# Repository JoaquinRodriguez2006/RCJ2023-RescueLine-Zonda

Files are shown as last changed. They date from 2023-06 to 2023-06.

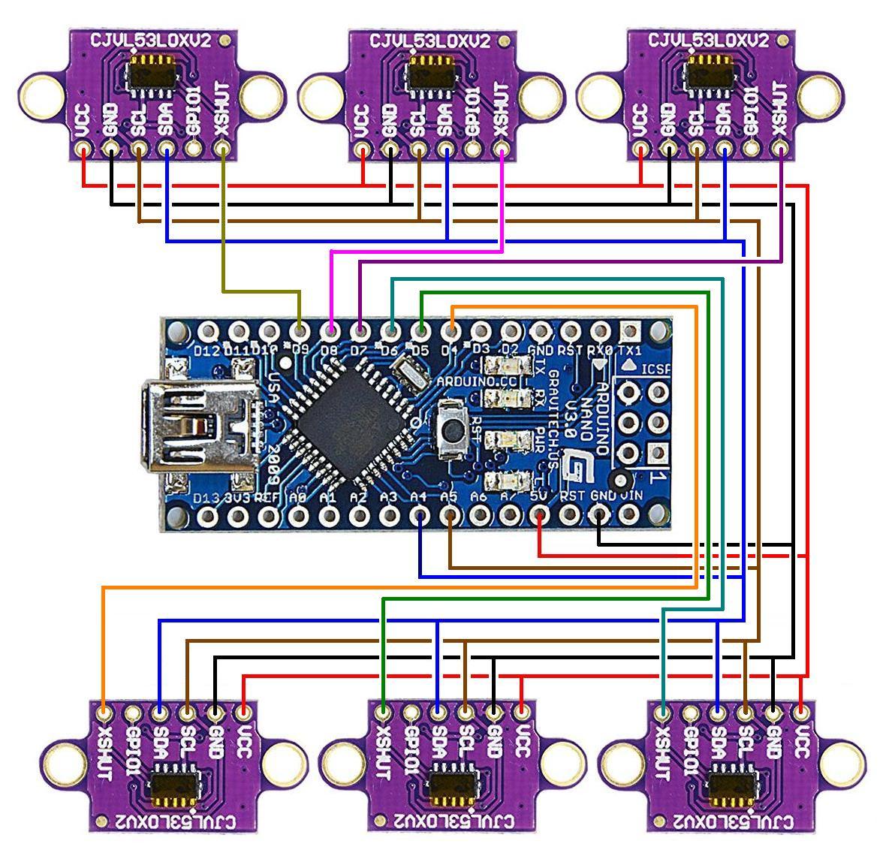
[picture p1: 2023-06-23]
Ejemplos Tof/Ejemplos usados/VL530X multi/VL530Xmulti.jpeg

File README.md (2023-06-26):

# Welcome to Team Zonda's Repo!
Hi there! We are Joaquín Rodríguez and Joaquín Argañaraz, from team Zonda IITA Salta, and we are excited to share our project with you! We are taking part in RCJ2023-RescueLine, and decided to create a robot that would push the limits by improving our Lego Spike Prime robot as much as possible. To do this, we developed a communication protocol between the Lego Spike and an Arduino Nano, which controls four Time-of-Flight sensors used to detect obstacles and walls, as well as some servos that operate the claw we use to pick the victims up! For further details, check out our Team Description Paper down below:

TDP Zonda: [tdp_zonda.pdf](https://github.com/JoaquinRodriguez2006/RCJ2023-RescueLine-Zonda/files/11843032/tdp_zonda.pdf)

or, to see the whole development process, feel free to look for anything you might need in our Engineering Journal!

Engineering Journal Zonda: [ZondaTeam.EngineeringJournal.pdf](https://github.com/JoaquinRodriguez2006/RCJ2023-RescueLine-Zonda/files/11843184/ZondaTeam.EngineeringJournal.pdf)

From codes to custom boards, everything in this project is open source and we hope you can feel inspired by it and contribute or replicate it and improve it on your own!! We would love to see this project and the innovations it features implemented in your robots!! Keep in mind, however, that this repo is under an MIT License, which gives you access to everything, yet asks you to give credits to the creators.

## Components
In order to make this possible, we are using electronic components, 3D-designed pieces and a Lego Spike robotics kit.

### Electronic Components
- Arduino Nano
- 4 Time-of-Flight sensors
- Standard Servo
- Mini Servo
- Custom board for Arduino Nano
- 2 custom boards for Time-of-Flight sensors (can hold up to 3 of them each, though we are only 2 on each side)
(Boards available at ```Placas Robotica``` )

### 3D Pieces
- Standard Servo Support
- MiniServo Support
- Claw (Left part & Right part)
- Adaptor Lego stick - servo
- Battery mount
- Claw Gears (Left & Right)

(You can check the .stl files here: ```3D Designs``` )

### Lego Spike Prime
- Lego Spike Prime educational robotics kit

## Codes
As we are using two different boards, two different codes are needed. The Lego Spike is coded in Python, while the Arduino uses C++. If you want to see the explanation of each code, function by funtion, feel free to check it out here: ```Documentation/Zonda IITA Salta. Codes/explanation.txt```
### Lego Spike Code
Uses Python and controls color sensors, motors and sends instructions to the Arduino, specifying what to do.
### Arduino Nano Code
Uses C++ and controls Time-of-Flight sensors and the servos operating the claw.

## PID Controller

## Communication Protocol

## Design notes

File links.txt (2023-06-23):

Lugares para indagar:

(Identificacion de pines)
https://www.facebook.com/groups/SPIKEcommunity/posts/1168406093537621/?mibextid=HsNCOg

(Documentacion pines)
https://github.com/GianCann/SpikePrimeHub

(I2C pins for arduino)
https://www.instructables.com/I2C-between-Arduinos/

(Raspberry HAT para controlar cosas de spike)
https://www.raspberrypi.com/news/raspberry-pi-build-hat-lego-education/

(conexion entre arduino y NXT)
https://www.dexterindustries.com/howto/connect-the-arduino-and-the-lego-mindstorms-together/

(conexion UART spike libreria)
https://antonsmindstorms.com/2022/11/18/lms-esp32-tutorials-part-0-how-to-get-started/

(libreria UART Remote arduino)
https://uartremote.readthedocs.io/en/latest/arduinouartremote.html

(MPY robots Tools)
https://github.com/antonvh/mpy-robot-tools

(conexion I2C entre EV3 y arduino)
https://www.dexterindustries.com/howto/connecting-ev3-arduino/

(I2C scanner)
https://playground.arduino.cc/Main/I2cScanner/

(Links utiles y conexion entre Raspberry Pico y Spike)
https://github.com/justMega/spikeResources

(Documentacion completa de Spike)
https://hubmodule.readthedocs.io/en/latest/port/

(Documentacion extra de Spike)
https://lego.github.io/MINDSTORMS-Robot-Inventor-hub-API/class_usb_vcp.html

(Conexion bluetooth entre Spikes y Raspberry)
https://github.com/bricklife/LEGO-Hub2Hub-Communication-Hacks

(Conexion bluetooth en mas profundidad)
https://github.com/maarten-pennings/Lego-Mindstorms

(Video Rasbperry Pi Zero y Spike)
https://www.youtube.com/watch?v=K0kwiPHDSnw

(Spike Comunication)
https://github.com/PhoBricks/SPIKE_communication

(Hub2Hub BLE)
https://www.facebook.com/groups/SPIKEcommunity/posts/1322920758086153/

(Documentacion Hub2Hub)
https://hubmodule.readthedocs.io/en/latest/hub2hub/

(Muchos Tutoriales con Arduino)
http://robojax.com/learn/arduino/

(Usar 2 VL53L0X (no lo usamos por mucho consumo de memoria))
http://robojax.com/learn/arduino/?vid=robojax_VL53L0X_multiple

(Usar 4 VL53L0X (no lo usamos por mucho consumo de memoria))
http://robojax.com/learn/arduino/?vid=robojax_VL53L0X_multiple_4

(I2C Scanner)
http://robojax.com/learn/arduino/?vid=robojax-I2C-scanner

(Usar 6 VL53L0X)
https://arduinoproyek.wordpress.com/2019/03/27/vl53l0x-multi-sensor/

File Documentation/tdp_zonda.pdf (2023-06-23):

ZONDA IITA SALTA | 1

# RoboCupJunior Rescue Line 2023

# Team Description Paper

## Zonda IITA Salta

Joaquín Rodríguez – Joaquín Argañaraz

Abstract – We are taking part in the Rescue Line category, where the robot needs to follow a line, avoiding any obstacles that may appear and turning left or right according to green tapes on the floor, until it reaches a rescue area. In this part, the robot will have to identify and classify alive and dead victims and rescue them, leaving them in a red or green corner located in the square. Our robot is able to do this efficiently and in record-breaking time (compared to previous versions of our project). This year, we took things way further and decided to use a Lego Spike kit, though we developed a communication protocol between the Spike and an Arduino Uno. This way, we couldn’t use Lego pieces only, and our robot features servos, 3D pieces and Time of Flight sensors, something never seen before.

I. INTRODUCTION
A. Team

Our team is rather small: it consists of only two people: Joaquín Rodriguez and Joaquín Argañaraz. We were both born in Salta and have been taking robotics classes since 2018 and 2017 respectively. Joaquín A. has taken part in RoboCup Junior 2019, in Australia, and has vast experience in educative robotics, as he’s been improving his skills and techniques over the years. He took part in Roboliga Nacional 2017 – Rescue Line, in Roboliga Nacional 2018 – Rescue Line, which took place in San Luis, Argentina, resulting in the first place, in Roboliga Nacional 2019 and in Roboliga Nacional 2022 – Rescue Line, with Zonda Team, which resulted in the first place and was able to represent Argentina in RoboCup Junior 2023. Joaquín Rodríguez, on the other hand, took part in Roboliga Nacional 2021 – Rescue Simulation, in RoboCup 2022 – Rescue Simulation, resulting in the 6th place and obtaining a Prize for the Best Teamwork. He also took part in Roboliga Nacional 2022, with Zonda Team, resulting in the first place, which lets the team represent our country in this competition.

II. PROJECT PLANNING

A. Overall Project Plan

Our aim for the competition is to improve the robot we’ve been building since September 2022. That original version of our project was able to navigate the whole scenario smoothly and with no complications at all. Nonetheless, we wanted to take things to the next level. We believe there was much more job to get done, so that is what we did. Our plan was to keep using Lego Spike for the main structure of the robot, yet we figured that some of its features didn’t live up to our expectations; we wanted a more precise distance sensor and a more professional claw. Keeping those things in mind, we realized that, even though Spike could perform such tasks, a dedicated tech pieces would do a better job. Therefore, we 3D printed a claw that would fit perfectly in our robot and bought Time of Flight sensors to replace the original Lego Spike distance sensor. To control all this gear, we initially intended to use a Teensy 4.1, which was impossible due to time issues. Therefore, we used an Arduino Nano instead.

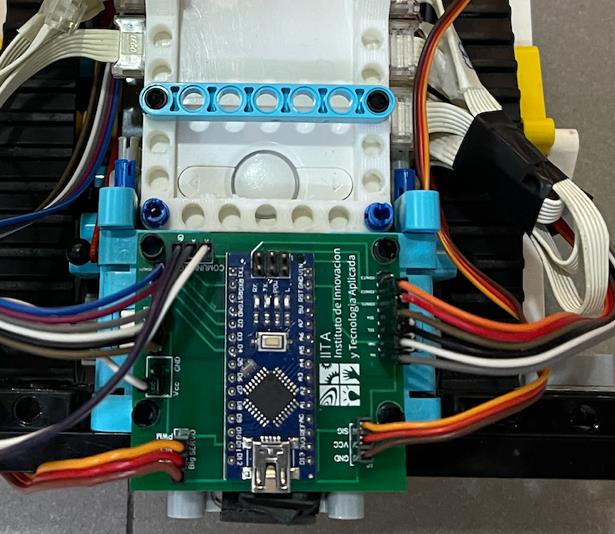
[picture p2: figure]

Fig.1: Arduino Nano fixed to the board.

Our plan was to use Lego Spike and Arduino Nano all together, integrated with each other, communicating both boards with a communication protocol of our own. Using a Lego minicomputer along with another board is something that none of us has ever seen before and we’re sure that, this could open a whole new world of possible things for our robot.

Apart | from | integrating | all | those
improvements to the project, there were some issues in the PID controller the robot uses to follow the line, so it was important to fix that as soon as possible.

Even though we are conscious the task the robot has to go over is rather complex and requires time and preparation, when we decided how to face this exercise, we chose to be ambitious. Time is not on our side and, in fact, is becoming a problem there is not enough time to implement everything we wanted on our robot. To begin with, we are choosing the first victims corner option, which is 0.5 cm tall instead of the second option, with 6cm of height. The original plan was to choose the second one, and the hardware selection was made according to that initial decision. Nonetheless, the robot would have needed a new color sensor to detect the wall and identify if it was red or green, which, even though was a good idea, couldn’t be implemented, as there are no free ports and there was literally no space for a new sensor.

Another important thing regarding our strategy is the rescue kit the robot has to pick up from the side of the line. We are going to have it put next to the line instead of carrying from the beginning of the task. Despite still not working properly and having very little time to fix it, our robot contains the necessary hardware to identify the cube and its claw is designed in a way that allows it to pick up the ball. Carrying the rescue kit from the beginning sounds logic and might be, in fact, a much cleverer idea. However, many pieces of the robot were designed specifically to be able to solve these kinds of situations and we want to show that.

B. Integration Plan

Our robot could be organized in various aspects: electronics, software, and hardware. The integration between all these areas is seamless and is barely noticeable, as we have organized everything in such a way that by pressing just a single button and connecting a single cable, it’s possible to get everything operating together.

We are working with a Lego Spike and an Arduino Nano, which means we have to establish some sort of connection between the two. To do so, after some time researching, we found out that it is possible to connect a Lego device to an Arduino board using a distance or color sensor, being the Lego Spike the host of the connection and the Arduino the slave, which was perfect for what we had planned. To establish such connection, we had to tear down a Lego Spike Distance Sensor and connect one side of the cable to the Arduino. Then we connected the Distance Sensor cable to the Spike. This way, the Arduino is able to send and receive messages to and from the Spike. Even though it is possible for the buffer to fill up and cause a lag between what the Spike is sending and what the Arduino is reading, this did not happen due to the implementation of a function that makes each board send messages only once, and not many times.

III. HARDWARE

A. Mechanical Design and Manufacturing

Lego Spike:

Our robot is built on a chassis made by Lego Spike pieces. From the caterpillars to the supports for the Spike Hub and the Arduino Nano, we have used the Lego Spike normal pieces that come in the box when it is first purchased, as it simplifies the building process, while still providing a reliable and solid base on which the other parts of the robot can be held.

3D Pieces

Apart from using the Lego Spike pieces that came with the robotics kit, we designed and printed many 3D pieces in our attempt to improve the claw mechanism.

Firstly, this robot features a claw (Fig.
2) that allows it to pick the victims and the rescue kit with no problems at all, thanks to its big lip at the bottom. This claw was not made by us; we found the design online (ap. 1) and decided to use it. however, the claw on the robot isn't the same as the one on the Internet. In fact, it looks like a completely different piece, as we've modified it in order to make it more functional to our needs. The changes include: 1) a lip that helps it pick up the rescue kit, 2) an increase in the height of the upper part of the claw (the claw wasn't long enough, and it didn't reach he ground, which made the process of picking the ball and the cube up a lot more complicated. Therefore, even though we could've made the claw a little bit taller, we decided to add some inches in the upper part, as it was the one that would mean the least increase in weight) and 3) reinforcements of certain pieces that are likely to break, like structural slim sticks and the part of the claw where we screw it to the main structure, as it was too tall, but too thin.

Fig. 2: The completely redesigned claw the robot features. It has a big lip at the bottom. It is 9 mm height, which, according to our measurements, is the biggest the down lip can be in order to be able to pick the ball up smoothly while still being able to lift the rescue kit: the servo makes pressure, and the down lips provide with enough surface for the cube to be lifted while being kept tight between the two claws. When the claw is lifting, the rescue kit eventually falls into the claws.

The claw is mounted on a 3D-designed support that does not only support the claw, but also the servo that operates the whole lifting and lowering mechanism. This piece was completely designed by us, and, even though exact measurements were taken, many versions had to be made in order to find the

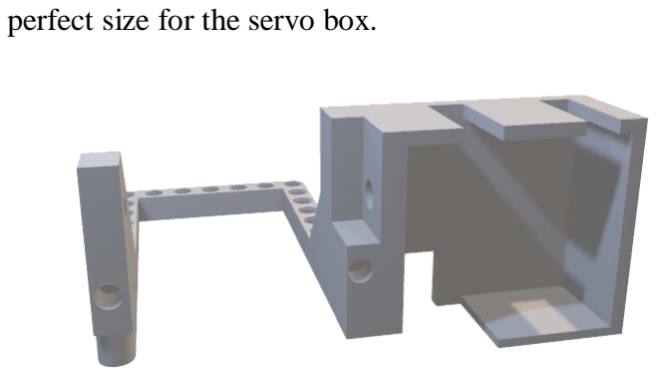
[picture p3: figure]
perfect size for the servo box.

Fig. 3: Standard Servo Support holds the standard servo, which is responsible of controlling the lifting and lowering of the claw. Hence, the piece has space for a horizontal stick that will receive the rotation of the servo and help with the movement of the claw.

Fig. 4: Adaptor that connects the horizontal stick to the servo.

We needed a piece to hold the servo that opens and closes the claw, as well as the claw itself. This piece needed to be strong, yet not too heavy, as it had to be able to be lifted and lowered by the standard servo. Keeping this in mind, we designed a piece that would have these requirements. This piece is rather long, helping the claw be a little separated from the robot’s structure when lowered, and contains a small box that holds the servo, as well as interlocking joints to place the gears that help with the claw’s movement.

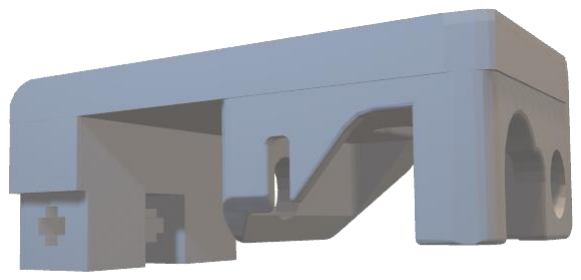
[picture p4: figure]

Fig. 5: Small Servo Support holds the small servo in a personalized servo box that keeps the small digital servo tight and ready to operate the claws. It also has little reliefs at the back so that the gears can fit in perfectly.

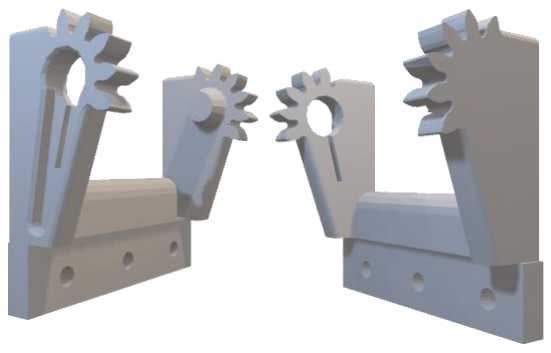
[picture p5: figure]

Fig. 6: The claw gear mechanism that allow it to open and close.

B. Electronic Design and Manufacturing

We are using two main types of sensors: three Lego Color Sensors and four Time of Flight sensors. Despite being used simultaneously, they are not controlled by the same board. The Lego Spike controls the Color Sensors and the Gyroscope and the Arduino Nano controls the ToFs sensors. In order for these two boards to work together, we needed to establish an Universal Asynchronous Receiver-Transmitter (UART) connection between them, which is possible after connecting Spike TX to Arduino RX and vice versa.

Lego Spike
Spike is the main board we are using and the host of the connection Spike-Arduino. The Lego Spike receives and sends information to the Arduino using one of its sensor cables. We had to cut a Distance Sensor cable in order to have access to the pins.

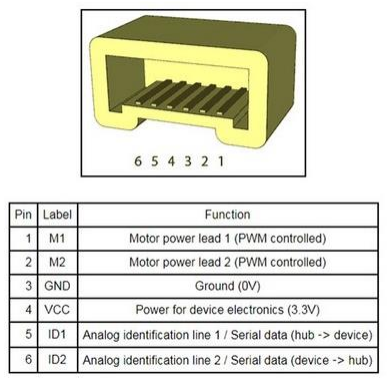
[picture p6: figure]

Fig. 7: Lego cable pinout

The pins include two PWM pins, two alimentation (VCC – GND) pins and two communication pins. The pins we are using for communication are RX, TX and GND. The pins in the cable are connected to Arduino RX, TX and GND (switching RX in the Lego cable to TX in the Arduino and RX in the Arduino to TX in the Lego cable). By doing this, we are able to send and receive information from and to the Arduino and Spike without clutter, as we’ve implemented a message request – answer system that we will explain in detail later.

Also, aiming to create a robot that isn’t completely full of disorganized cables and non-safe connections, we designed a board to hold the Arduino Nano and facilitate the connection with the Lego cable.

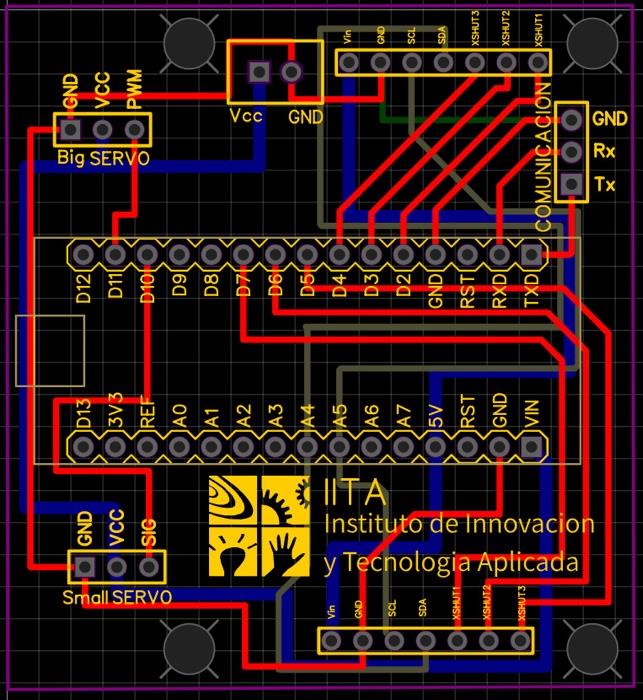
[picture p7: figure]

Fig. 8: The board that holds the Arduino in the middle and receives the cable connections on the sides.

Regarding sensors, we are using three Lego color sensors, which are symmetrically arranged under the robot.

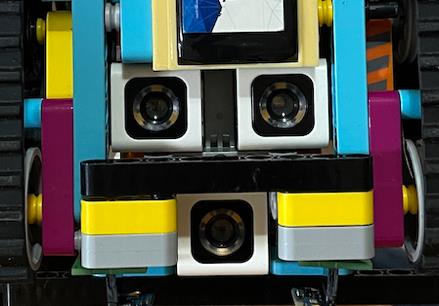
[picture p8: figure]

Fig. 9: Color sensors under the robot.

To detect things, we implemented a new technology for us, which is Time of Flight sensors (ToFs). They are fixed to a personalized board located in the front part of our robot.

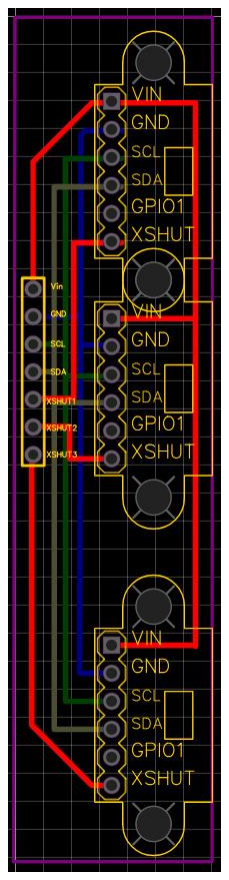
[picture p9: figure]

Fig. 10: Board that holds the Tine of Flight sensors. There are three spots for a ToF sensor, yet we are only using two and planning to add a third one in the future.

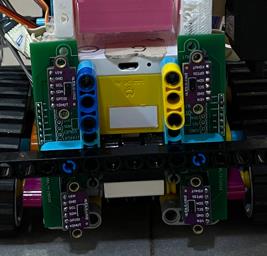
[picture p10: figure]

Fig. 11: Time of Flight boards located at the front of our robot.

IV. SOFTWARE

A. General Software Architecture

We have coded our robot in two different languages: we used Python for the Lego Spike and C++ for the Arduino Nano.

As we mentioned earlier, our robot consists of two different boards that need to communicate wirily. Hence, codes should be able to read the buffers, so as to know if there is anything it needs to know, and also send messages to the other board using a specific communication protocol. This communication protocol is explained in detail in the diagram below:

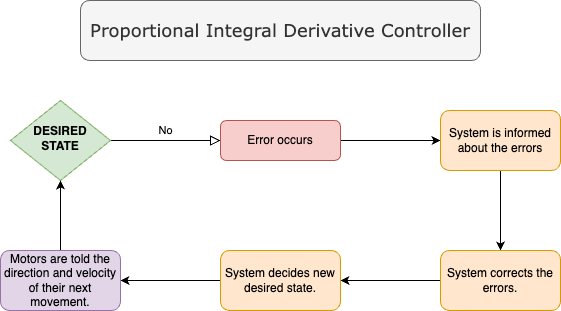
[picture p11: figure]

Diagram 1: Communication Protocol

Python Code
Our Python code is used in the Lego Spike Hub, which controls the motors and receives and process information from three Color Sensors and is responsible for the whole line-following part of the exercise, except for the obstacle, that needs the Time-of-Flight sensors. The algorithm used to follow the line
is | the | Proportional-Integral-Derivative
Controller (PID Controller) (Appendix, 1)

C++ Code
The C++ code operates the servo and receives and process the Time-of-Flight data. This code reads the state the Lego sends via UART messages and starts sending the Spike letter, depending on the state, according to what the sensors are seeing, (STATE = ‘line-follower’ → a: ‘go’, f: ‘stop’) (STATE = ‘obstacle’ → N: ‘nule’, R: ‘super close’, C: ‘close’, M: ‘very far’, L: ‘far’) (STATE = ‘rescue’ → U: ‘nule’, N: ‘near’, F: ‘far’). It also reads if the Spike has sent an order and, depending on the message the Lego Hub sends, lifts, lowers, opens, or closes the claw.
B. Innovative Solutions

UART Communication Protocol Arduino - Spike
A communication protocol between two completely different microcontrollers was implemented. Keeping in mind that it was necessary to connect those boards seamlessly, establishing a clean connection that would not clutter neither the Arduino
nor | the | Spike | buffers, | an | UART
communication protocol was developed. As it is known, UART connections use
serial | ports | to | receive | and | send
information. Therefore, knowing that both boards had to be capable of sending and receiving info, so as to maintain a human-like conversion, though not only using
complete | phrases, | sentences | and
paragraphs, but uppercase and lowercase letters in order to transmit instructions or states. As it has been stated before, the two boards are connecting via serial ports using
RX, | TX | and | GND | pins. | The
communication | protocol | is | possible
because of a Lego Distance Sensor cable that has been cut, so that the connector that goes right in the Lego Spike Hub could be on one side of the cable (allowing it to connect to the hub like a normal sensor) and the pins could be ready to be plugged in the Arduino Nano. This way, the Arduino functions almost like a normal sensor (or at least that is how the Spike understands the information it sends), except for the fact that, of course, must be coded in a different language and that it is not, by all means, a normal sensor. It could be considered a ‘mega-Lego-sensor’, as it is in charge of many important tasks: operating everything related to the claw

(opening, closing, lowering and lifting it) and checking the robot does not crash into obstacles or walls by controlling the data collected by Time-of-Flight sensors. This communication protocol is also effective due to the highly-debugged code, which has a function that prevents buffers from cluttering with messages.

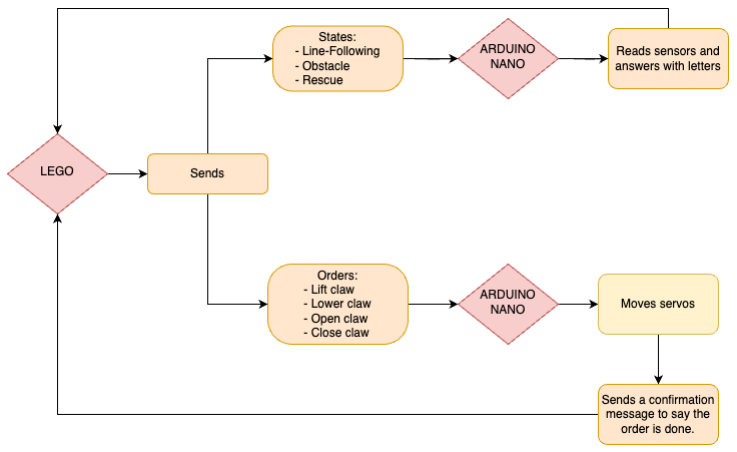
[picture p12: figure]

Diagram 2: Communication Protocol.

### Integration

In order to make this integration even better, the Arduino is not working alone; many Time-Of-Flight sensors depend on it, as well as two servos located above and at the side of the claw. For us to integrate those non-Lego pieces into the design and aesthetics of the main structure, it was necessary to adapt some pieces. Therefore, some crucial parts of the robot, such as the claw mount, are fixed to the Lego Brick because they have been 3D-Printed, and the design met Lego measurements and sizes.

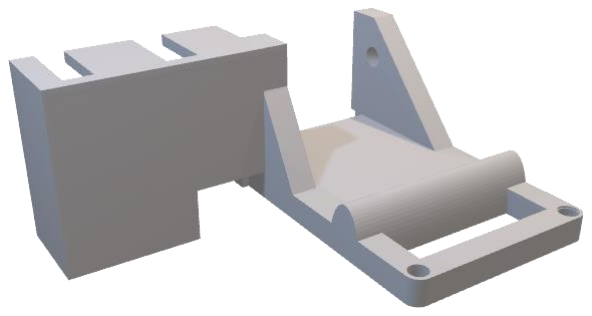
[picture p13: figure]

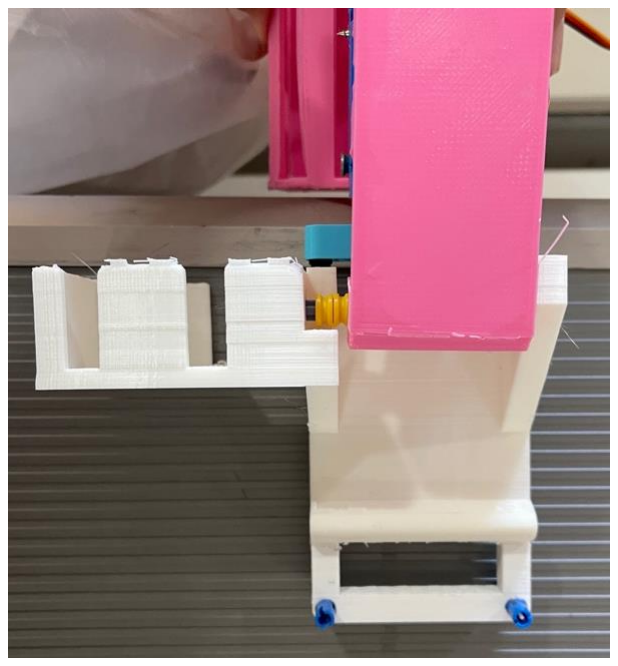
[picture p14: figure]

Figs. 12 & 13: The claw mount that is fixed to the Lego Brick

V. PERFORMANCE
EVALUATION
Our robot is able to follow the line slowly, though precisely and never steps out of
line. | Obstacles, | ramps, | seesaws,
speedbumps are solved. It is also able to deposit the Rescue Kit in the rescue area in a decent way. Even though it sometimes struggles with ramps, it is sure that the robot will overcome it. The most complicated part is, for sure, the rescue area, which is still under testing. Zonda IITA Salta robot is able to identify victims, rescue and deposit them in a corner with no complications. However, we did not add anything so as for the robot to be able to know whether it is an alive or a dead victim. Nonetheless, it recognizes red and green corners and it chooses where to deposit one victim or the other using a random() function.

VI. CONCLUSION
To sum up everything that has been stated so far, Zonda IITA Salta robot is able to follow the line seamlessly and with no complications, except for the ramp, sometimes. This robot is innovating by
including | a | Lego | – | Arduino
communication protocol which allows both boards to work together by sending and receiving messages that command states or orders. Also, we are implementing a new technology for us, which are Time of Flight sensors. In order to integrate them to the general structure of the robot, we designed boards, which are not exclusive for ToFs. There is also a custom board for the Arduino Nano. These boards help with cable management, as there are not disorganized cables around the robot, and also with safety, due to the fact that these cables connected to the boards will not fall off, causing problems.

This is, overall, a good, reliable robot that might be a little slow sometimes, but it is surely going to perform decently.

REFERENCES

- https://scholar.google.com/scholar_url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 (https://scholar.google.com/scholar_url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)
- https://en.wikipedia.org/wiki/PID_controller
- http://ethesis.nitrkl.ac.in/5405/1/109EI0326.pdf
- https://www.ni.com/es-cr/shop/labview/pid-theory-explained.html
- https://www.analog.com/en/analog-dialogue/articles/uart-a-hardware-communication-protocol.html
- https://www.circuitbasics.com/basics-uart-communication/
- https://www.geeksforgeeks.org/universal-asynchronous-receiver-transmitter-uart-protocol/

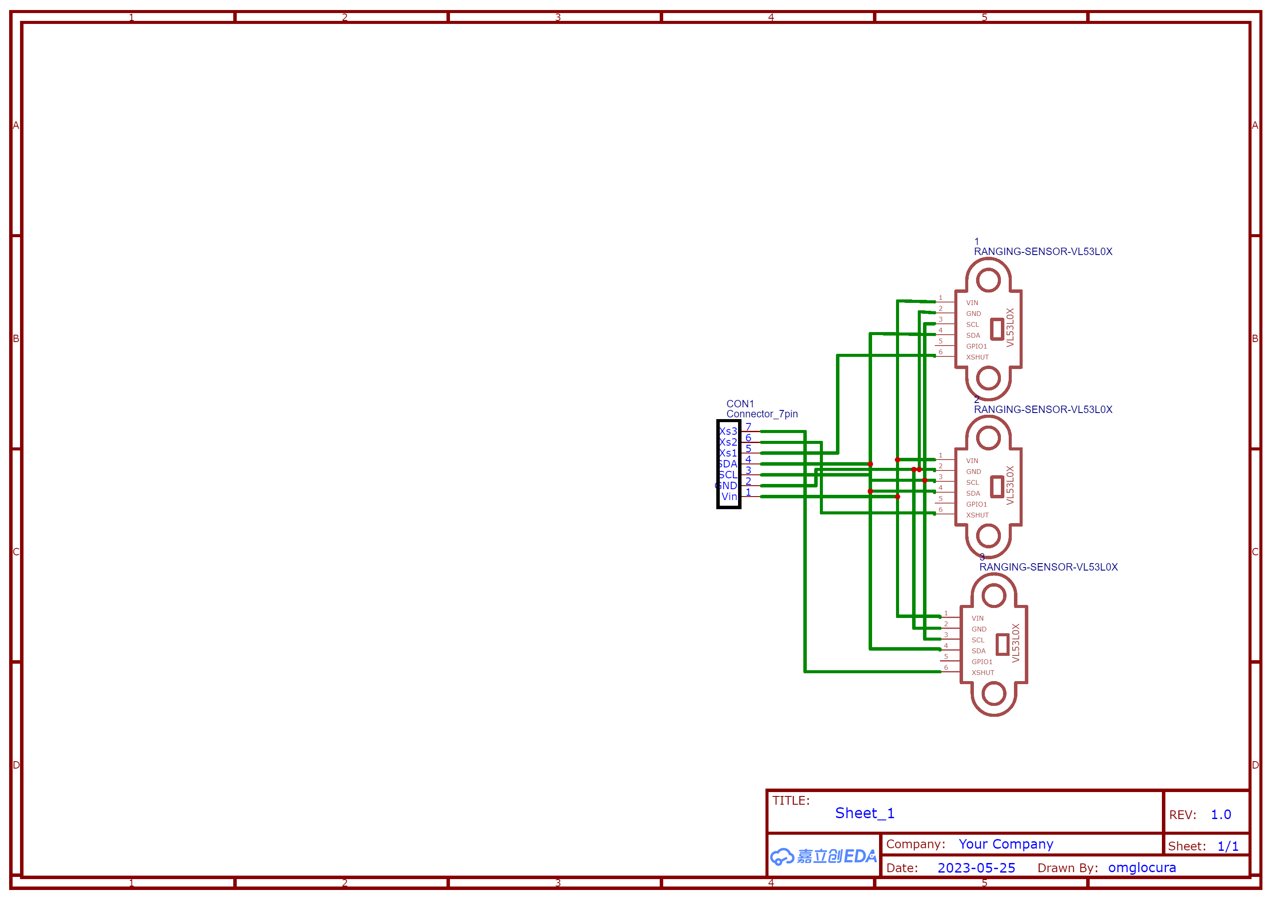
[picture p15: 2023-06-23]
Placas Robotica/PCB ToF/Schematic_Pcb Tof Robocup Joaquin_2023-06-20.png

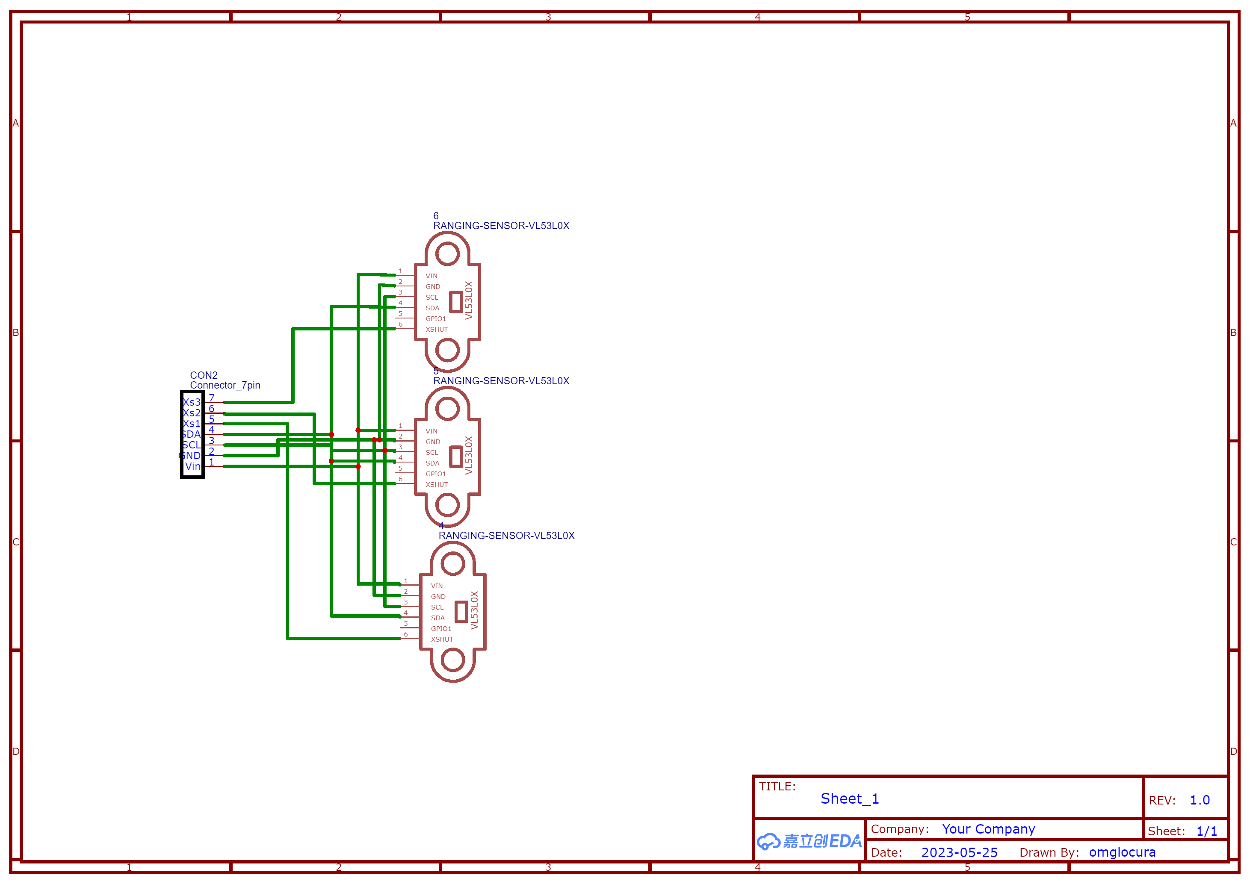
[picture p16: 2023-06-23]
Placas Robotica/PCB ToF Espejo/Schematic_Espejo Pcb tof_2023-06-20.png

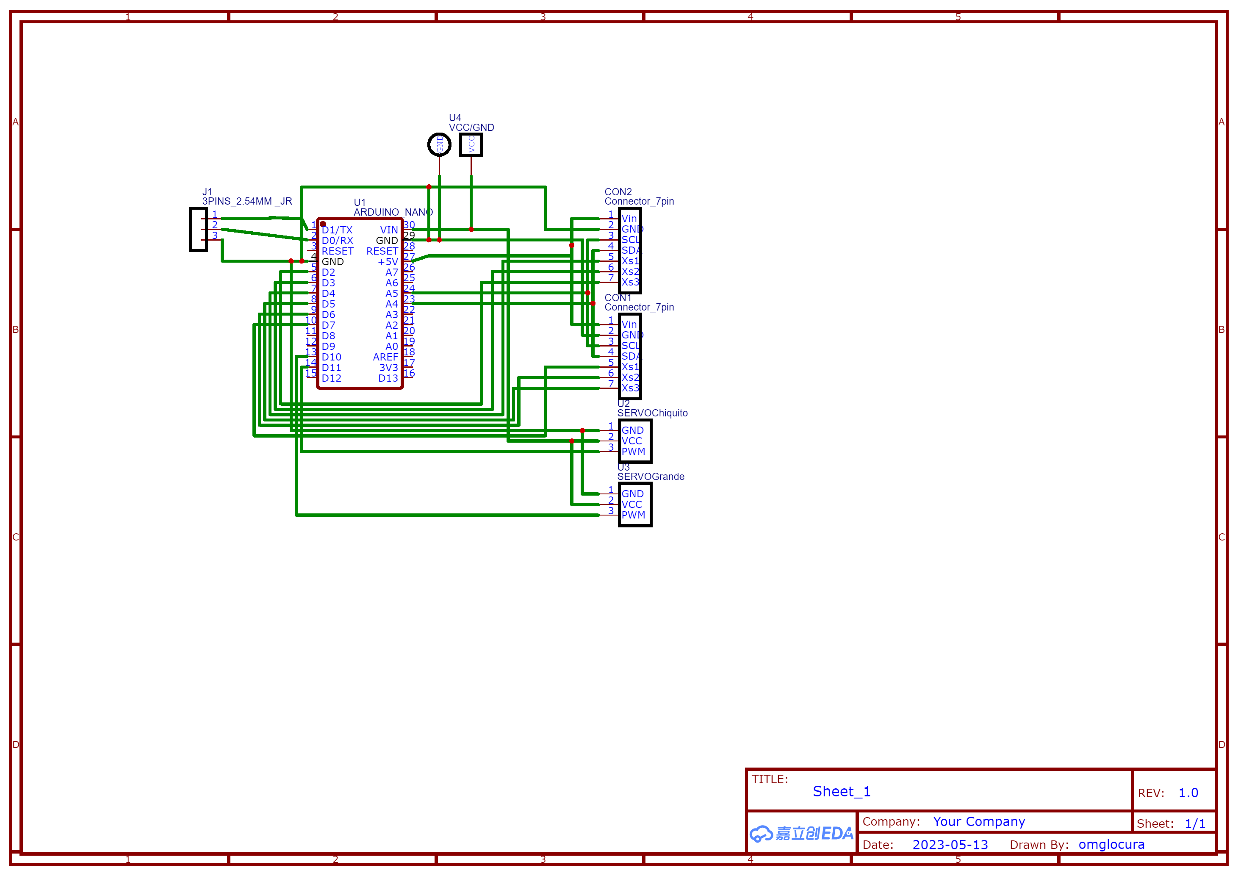
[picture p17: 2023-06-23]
Placas Robotica/PCB Arduino/Schematic_robotica_2023-06-20.png

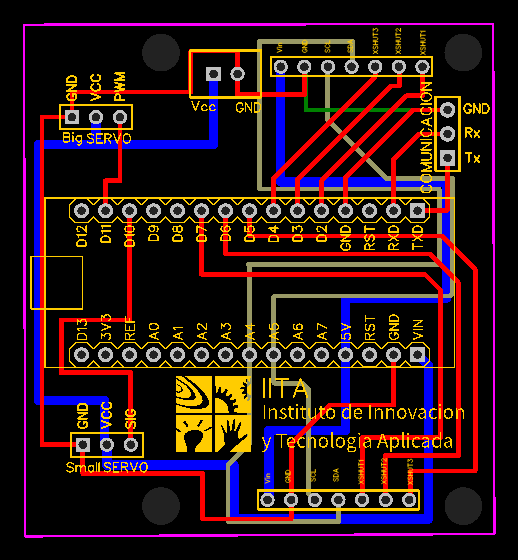
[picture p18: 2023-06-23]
Placas Robotica/PCB Arduino/PCB_PCB_Arduino_IITA_ROBOCUP_2023-25-05_2023-06-20.png

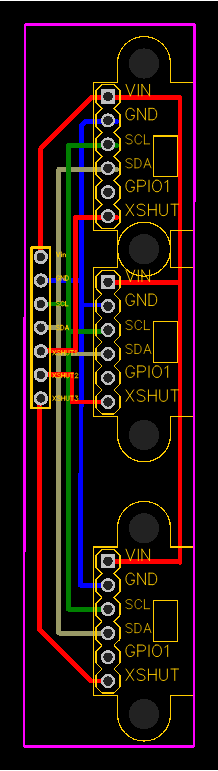
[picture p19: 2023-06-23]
Placas Robotica/PCB ToF/PCB_PCB_Tof_IITA_ROBOCUP_2023-25-05_2023-06-20.png

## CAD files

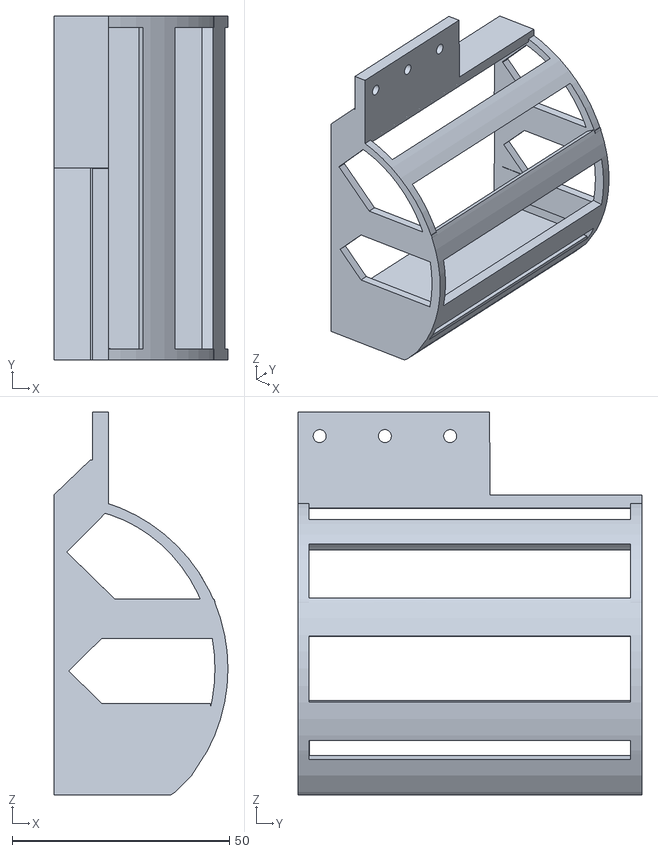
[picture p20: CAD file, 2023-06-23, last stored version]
3D Designs/RCJ2023-Claws 2.0-R.stl
40.0 x 79.1 x 88.0

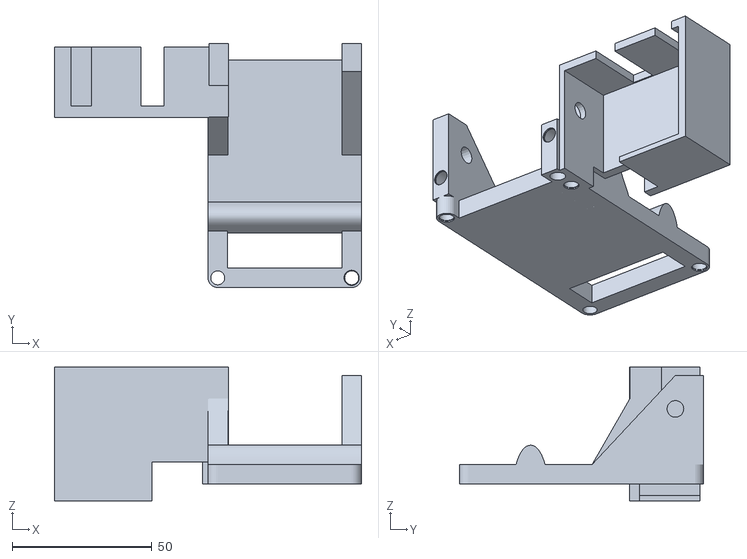
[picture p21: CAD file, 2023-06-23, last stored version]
3D Designs/RCJ2023-StandardServoBox4.0.stl
110.0 x 87.5 x 48.0

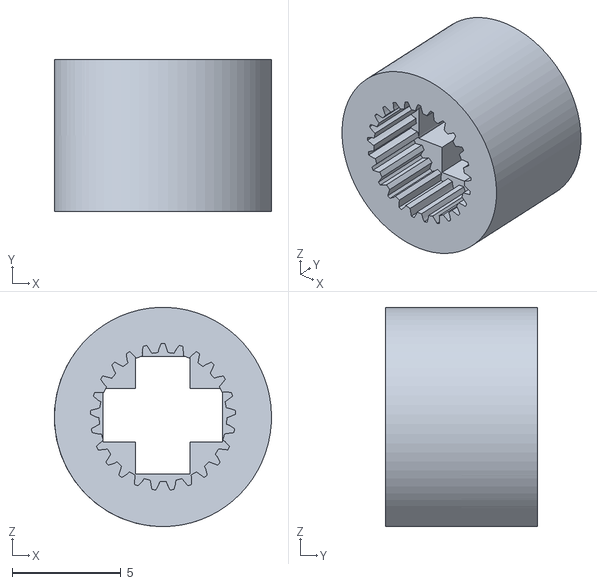
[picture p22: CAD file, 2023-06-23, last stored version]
3D Designs/RCJ2023-Adaptor.stl
10.0 x 7.00 x 10.1

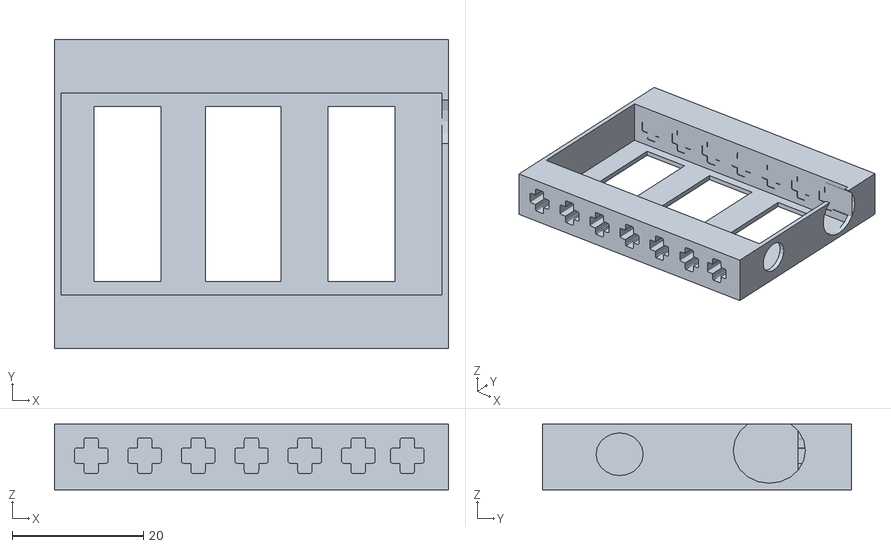
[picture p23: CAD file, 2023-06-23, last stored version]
3D Designs/RCJ2023-BatteryMount.stl
60.0 x 47.0 x 10.0

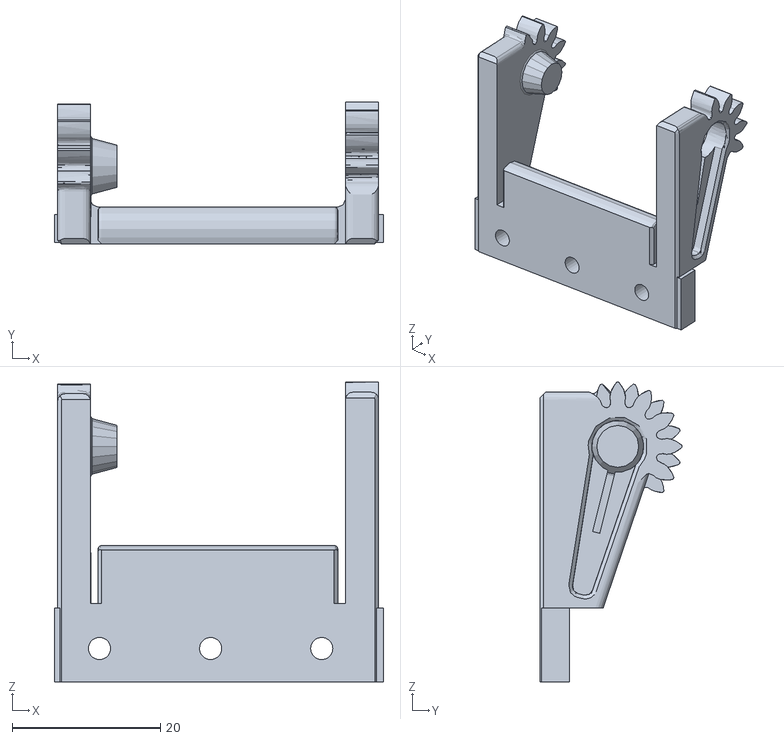
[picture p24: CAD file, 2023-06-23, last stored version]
3D Designs/RCJ2023-ClawGears-L.stl
44.4 x 19.2 x 40.5

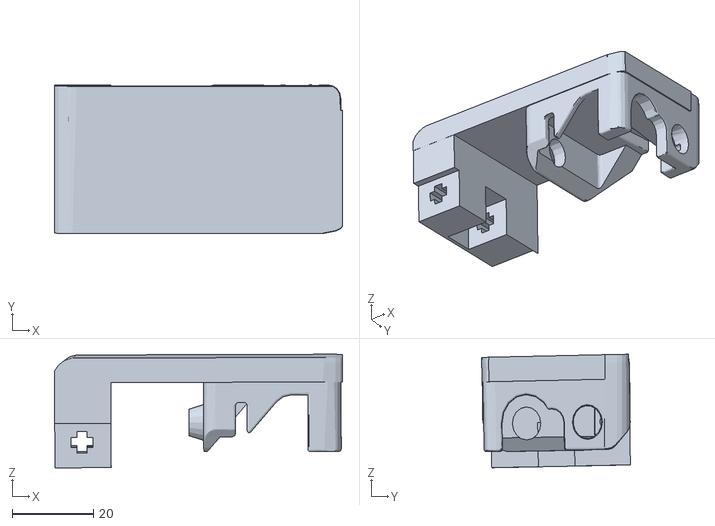
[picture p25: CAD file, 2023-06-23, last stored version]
3D Designs/RCJ2023-MiniServoBox3.0.stl
71.0 x 36.7 x 28.0

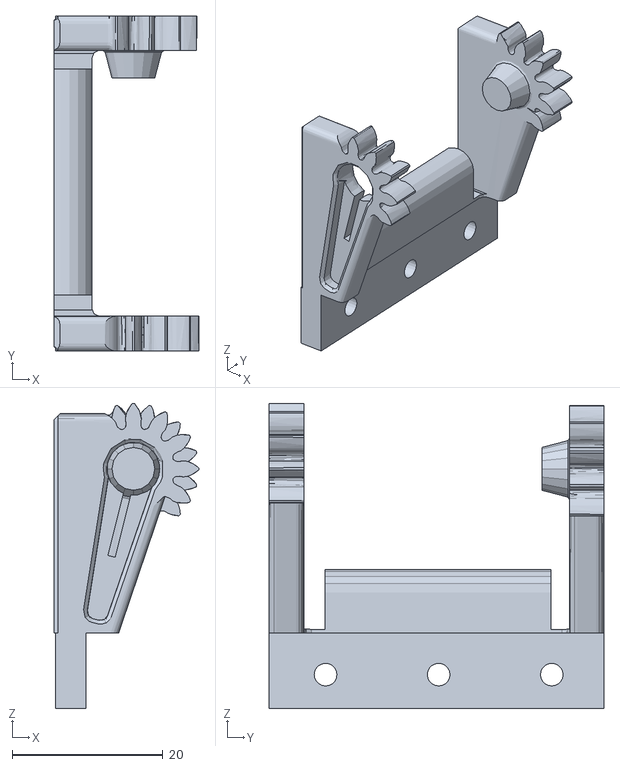
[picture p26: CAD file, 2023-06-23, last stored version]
3D Designs/RCJ2023-ClawGears-R.stl
19.2 x 44.4 x 40.5

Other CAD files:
3D Designs/RCJ2023-Claws 2.0-L.stl

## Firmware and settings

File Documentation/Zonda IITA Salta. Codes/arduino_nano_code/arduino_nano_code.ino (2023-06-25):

#include <Wire.h>
#include <VL53L0X.h>
#include <Servo.h>

Servo Servin;
Servo Servo;

int t = 30; // Tiempo en milisegundos para los servos

VL53L0X sensor_ru;   // Sensor Right-up
VL53L0X sensor_rd;   // Sensor Right-down
VL53L0X sensor_lu;   // Sensor Left-up
VL53L0X sensor_ld;   // Sensor Left-down

int a;
int b;
int c;
int d;

int pin_ru = 2;
int pin_rd = 3;

int pin_lu = 7;
int pin_ld = 6;

int cont = 0;

bool detectar = false;
bool mov_big_up = false;
bool mov_big_down = false;
bool mov_small_open = false;
bool mov_small_closed = false;

String st1;

void setup() {
  // Begin the Serial at 9600 Baud
  Serial.begin(115200);
  Servin.attach(10);
  Servo.attach(11);
  pinMode(13,OUTPUT);
  
  Servin.write(70);
  Servo.write(160);
 
////////////////////////////////////////////////////

  pinMode(pin_lu, OUTPUT);
  pinMode(pin_ld, OUTPUT);
  pinMode(pin_rd, OUTPUT);
  pinMode(pin_ru, OUTPUT);
  digitalWrite(pin_ru, LOW);
  digitalWrite(pin_rd, LOW);
  digitalWrite(pin_ld, LOW);
  digitalWrite(pin_lu, LOW);

  delay(500);
  Wire.begin();
  // Serial.begin (9600);

// Pin Right Up
  digitalWrite(pin_ru, HIGH);
  delay(150);
  // Serial.println("00");
  sensor_ru.init(true);

  // Serial.println("01");
  delay(100);
  sensor_ru.setAddress((uint8_t)01);
  // Serial.println("02");

// Pin Right Down
  digitalWrite(pin_rd, HIGH);
  delay(150);
  sensor_rd.init(true);
  // Serial.println("03");
  delay(100);
  sensor_rd.setAddress((uint8_t)02);
  // Serial.println("04");

// Pin Left Down
  digitalWrite(pin_ld, HIGH);
  delay(150);
  sensor_ld.init(true);
  // Serial.println("05");
  delay(100);
  sensor_ld.setAddress((uint8_t)03);
  // Serial.println("06");

// Pin Left Up
  digitalWrite(pin_lu, HIGH);
  delay(150);
  // Serial.println("07");
  sensor_lu.init(true);

  // Serial.println("08");
  delay(100);
  sensor_lu.setAddress((uint8_t)04);
  // Serial.println("09");

  sensor_ru.startContinuous();
  sensor_rd.startContinuous();
  sensor_ld.startContinuous();
  sensor_lu.startContinuous();

/////////////////////////////////////////////////////

}

void loop() {
  if (Serial.available() > 0) {
    st1 = Serial.readStringUntil('\n'); //Read the serial data and store in var
    st1.trim();
    if(st1 == "Seguidor" || st1 == "Obstaculo" || st1 == "Rescue"){
      detectar = true;
    }
    else if (st1 == "Mov_Big_Up"){
      mov_big_up = true;
    }
    else if (st1 == "Mov_Big_Down"){
      mov_big_down = true;
    }
    else if (st1 == "Mov_Small_Open"){
      mov_small_open = true;
    }
    else if (st1 == "Mov_Small_Closed"){
      mov_small_closed = true;
    }
    else{
      detectar = false;
      mov_big_up = false;
      mov_big_down = false;
      mov_small_open = false;
      mov_small_closed = false;
    }
  }

  while (Serial.available() == 0){
    if (detectar){
      update();
    }
// LINE - FOLLOWER
      if (st1 == "Seguidor"){ // Preguntar con los sensores de abajo y medio
        digitalWrite(13,LOW);
        if((a > 110) && (b > 110)){
          Serial.write('A');  // Andar
          cont = 0;
        }
        if((a < 110) || (b < 110)){
          // Serial.println(a);
          // Serial.println(b);
          cont = cont+1;
          if (cont > 3){
            Serial.write('F');  // Frenar
            cont = 0;
          }
        }
      }

// RESCUE
  // Explore
      if (st1 == "Rescue"){
        if((a > 200) && (b > 200)){
          Serial.write('u');  // Nule
        }
      else if((a < 80) && (b < 80)){
          Serial.write('n');  // Near
        }
      else if((a < 100) && (b < 100)){
        Serial.write('a');  // Always
      }
      else if((a < 140) && (b < 140)){
        Serial.write('f');  // Far
      }

  // Despositing the cube
      if (st1 == "Rescue_dc"){ // Rescue Cube Down: It is basically an order for the Arduino to deposit the cube
        Deposit_Cube();
        // if Deposit_Cube(){
        //   Serial.write('CONFIRMED');
        // }
        // else{
        //   Serial.write('ERROR OCURRED');
        // }
      }
    
  // Rescuing the Victim
      if (st1 == "Spotted_Victim") {
        Rescuing_Victim();
        // if Rescuing_Victim() {
        //   Serial.write('CONFIRMED');
        // }
        // else{
        //   Serial.write('ERROR OCURRED');
        // }
      }

  // Looking for the victim
      if (st1 == "Rescue_lv") {
        if((c > 200) && (d > 200)){
          Serial.write('U');  // Nule
          }
        else if((c > 80) && (d > 80)){
          Serial.write('N');  // Near
          }
        else if((c > 100) && (d > 100)){
          Serial.write('A');  // Always
          }
        else if((c > 140) && (d > 140)){
          Serial.write('F');  // Far
          
      }        
      
// OBSTACLE
      }      
      if (st1 == "Obstaculo"){ // Preguntar con cualquier sensor
        digitalWrite(13,HIGH);
        if((a > 200) && (b > 200)){
          Serial.write('N');  // No Detecta
        }
        else if((a < 65) || (b < 65)){
          Serial.write('R');  // Re Cerca
        }
        else if((a < 80) && (b < 80)){
          Serial.write('C');  // Cerca
        }
        else if((a < 100) && (b < 100)){
          Serial.write('S');  // Siempre
        }
        else if((a < 140) && (b < 140)){
          Serial.write('L');  // Lejos
        }
        else if((a < 180) && (b < 180)){
          Serial.write('M');  // Muy lejos
        }
      }
    }
    else if (mov_big_up){
      Mov_Servo(t,160);
      // delay(400);
      Serial.write('O');   // OK arriba  
    }
    else if (mov_big_down){
      Mov_Servo(t,30);
      // delay(400);
      Serial.write('O');   // OK abajo
    }
    else if (mov_small_open){
      Mov_Servin(t,10);
      // delay(400);
      Serial.write('O');   // OK abierto
    }
    else if (mov_small_closed){
      Mov_Servin(t,70);
      // delay(400);
      Serial.write('O');   // OK cerrado
    }


    mov_big_up = false;
    mov_big_down = false;
    mov_small_open = false;
    mov_small_closed = false;
    detectar = false;
    break;
  }
}


void update(){
  a = sensor_ru.readRangeContinuousMillimeters();
  b = sensor_lu.readRangeContinuousMillimeters();
  c = sensor_rd.readRangeContinuousMillimeters();
  d = sensor_ld.readRangeContinuousMillimeters();
}

void Mov_Servo(int tiempo, int destino){ // Movimiento regulado en el tiempo del Servo Grande
  if (Servo.read() > destino){           
    for (int pos = Servo.read(); pos >= destino; pos -= 1) {    // Si la posicion del servo es mayor al de destino va a restar
      Servo.write(pos);          
      delay(tiempo);                     
    }
  }
  else{
    for (int pos = Servo.read(); pos <= destino; pos += 1) {    // Si la posicion del servo es menor al de destino va a sumar
    Servo.write(pos);              
    delay(tiempo);                       
    }
  }
}

void Mov_Servin(int tiempo, int destino){ // Movimiento regulado en el tiempo del Servo Chiquito
  if (Servin.read() > destino){           
    for (int pos = Servin.read(); pos >= destino; pos -= 1) {    // Si la posicion del servo es mayor al de destino va a restar
      Servin.write(pos);          
      delay(tiempo);                     
    }
  }
  else{
    for (int pos = Servin.read(); pos <= destino; pos += 1) {    // Si la posicion del servo es menor al de destino va a sumar
    Servin.write(pos);              
    delay(tiempo);                       
    }
  }
}

void Deposit_Cube(){
  Mov_Servo(t,30);
  Mov_Servin(t,10);
  Mov_Servo(t,160);
  Mov_Servin(t,70);
}

void Rescuing_Victim() {
  Mov_Servo(t,90);
  Mov_Servin(t,10);
  Mov_Servo(t,30);
  Mov_Servin(t,70);
  Mov_Servo(t,160);
}

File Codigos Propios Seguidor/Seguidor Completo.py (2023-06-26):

from spike import PrimeHub, LightMatrix, Button, StatusLight, ForceSensor, MotionSensor, Speaker, ColorSensor, App, DistanceSensor, Motor
from spike.control import wait_for_seconds, wait_until, Timer
from spike import MotorPair
import math
from hub import port

import hub as advancedHub
import time
import math
import random

hub = PrimeHub()
timer = Timer()


# COMUNICACION
port.E.mode(port.MODE_FULL_DUPLEX)
b=port.E
wait_for_seconds(1)
b.baud(115200)
wait_for_seconds(1)

# MOTORES
motor_pair = MotorPair('C', 'A')
motor_pair.set_motor_rotation(3.2 * math.pi,'cm')

# SENSORES
sen_1 = ColorSensor("B")
sen_2 = ColorSensor("D")
sen_3 = ColorSensor("F")

# PID
global error_previo
global integral

error = 0
error_previo = 0
integral = 0
derivada = 0
proporcional = 0
kp = 3.95    # 3.95 antes
ki = 0.02
kd = 0.4
salida = 0


global s

def update():
    global r1,g1,b1,ov1
    global r3,g3,b3,ov3

    global col_1
    global col_3

    r1,g1,b1,ov1 = sen_1.get_rgb_intensity()
    r3,g3,b3,ov3 = sen_3.get_rgb_intensity()

    if r1 + 20 < g1 > b1 and g1 < 220:# g1 = 205
        # print('MANZANA: ',r1,g1,b1)
        col_1 = 'green'
    elif r1 + 20 < g1 > b1 + 10 and g1 < 260:
        # print('AGROPECUARIO: ',r1,g1,b1)
        col_1 = 'green'
    elif r1 > 700 and g1 > 700 and b1 > 700:
        col_1 = 'plateado'
    else:
        # print('PERA: ',r1,g1,b1)
        col_1 = 'no'
        # print(r1,g1,b1)

    if r3 + 20 < g3 > b3 and g3 < 220: # g3 = 205
        # print('Verde: ',r3,g3,b3)
        col_3 = 'green'
    elif r3 + 20 < g3 > b3 + 10 and g3 < 260:
        # print('Verde blanquesino',r3,g3,b3)
        # print('a')
        col_3 = 'green'
    elif r3 > 700 and g3 > 700 and b3 > 700:
        col_3 = 'plateado'
    else:
        # print('no: ',r3,g3,b3)
        col_3 = 'no'

    global c1
    global c3

    c1 = sen_1.get_color()
    c3 = sen_3.get_color()


    global luz_1
    global luz_2
    global luz_3

    luz_1 = sen_1.get_reflected_light()
    luz_2 = sen_2.get_reflected_light()
    luz_3 = sen_3.get_reflected_light()


def giro_90_der():
    motor_pair.start_tank(0,0)
    # wait_for_seconds(1)
    hub.motion_sensor.reset_yaw_angle()
    while (hub.motion_sensor.get_yaw_angle() < 83):
        motor_pair.start_tank(30,-30)
    motor_pair.start_tank(0,0)
    # wait_for_seconds(1)
    angle = hub.motion_sensor.get_yaw_angle()
    # print('Angulo:', angle)

def giro_90_izq():
    motor_pair.start_tank(0,0)
    # wait_for_seconds(1)
    hub.motion_sensor.reset_yaw_angle()
    while (hub.motion_sensor.get_yaw_angle() > -83):
        motor_pair.start_tank(-30,30)
    motor_pair.start_tank(0,0)
    # wait_for_seconds(1)
    angle = hub.motion_sensor.get_yaw_angle()
    # print('Angulo:', angle)

def giro_180_der():
    giro_90_der()
    giro_90_der()
    motor_pair.move_tank(0.7,'cm',30,-30)

def giro_180_izq():
    giro_90_izq()
    giro_90_izq()
    motor_pair.move_tank(0.7,'cm',-30,30)

def girar_num_grados_der(num):
    hub.motion_sensor.reset_yaw_angle()
    while (hub.motion_sensor.get_yaw_angle() < num):
        motor_pair.start_tank(30, -30)
    motor_pair.start_tank(0, 0)
    hub.motion_sensor.reset_yaw_angle()

def posible_verde():
    pera = 0
    hub.motion_sensor.reset_yaw_angle()
    while hub.motion_sensor.get_yaw_angle() < 10:
        update()
        motor_pair.start_tank(60,-60)
        if col_1 == 'green' or col_3 == 'green':
            motor_pair.start_tank(0,0)
            pera = 1
            break
    motor_pair.start_tank(0,0)
    wait_for_seconds(0.1)
    if pera == 0:
        hub.motion_sensor.reset_yaw_angle()
        while hub.motion_sensor.get_yaw_angle() > -10:
            motor_pair.start_tank(-60,60)
        motor_pair.start_tank(0,0)
        wait_for_seconds(0.1)
        hub.motion_sensor.reset_yaw_angle()
        while hub.motion_sensor.get_yaw_angle() > -10:
            update()
            motor_pair.start_tank(-60,60)
            if col_1 == 'green' or col_3 == 'green':
                motor_pair.start_tank(0,0)
                pera = 1
                break
        motor_pair.start_tank(0,0)
        wait_for_seconds(0.1)
        if pera == 0:
            hub.motion_sensor.reset_yaw_angle()
            while hub.motion_sensor.get_yaw_angle() < 10:
                motor_pair.start_tank(60,-60)
            motor_pair.start_tank(0,0)
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

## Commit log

2023-03-26 Agrego manual para LIpo de 2Celdas 7.4v
2023-06-20 add libraries & PCBs
2023-06-23 add 3d pieces
    [RCJ2023-Adaptor.stl, RCJ2023-BatteryMount.stl, RCJ2023-ClawGears-L.stl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]
2023-06-23 add documentation
    [RCJ2023-Adaptor.stl, RCJ2023-BatteryMount.stl, RCJ2023-ClawGears-L.stl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]
